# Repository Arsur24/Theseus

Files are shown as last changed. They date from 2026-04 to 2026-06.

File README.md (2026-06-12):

# Theseus
This repository will cover the documentation for RoboCup Junior Maze team Theseus.
The repository is structured into 3 main categories: mechanical, electronics, and coding.

## Overview of system architecture
Our team participates in the RoboCup Junior Maze challenge, where the goal is to navigate throughout a randomized maze, detect victims, dispense rescue packages, and navigate the maze. From a high-level view, we utilize a hybrid control architecture, which is comprised of a Deliberative layer and a reactive layer. The Deliberative layer focuses on the high-level planning of the robot's movement, such as mapping and pathfinding, whilst the reactive layer focuses on keeping the robot's movement stable, and also to detect victims. 
## Electronics
Our team has experimented with a variety of different sensors and electronics, and we found that I2C sensors produce the best results due to the organizational advantages of utilizing a single communications protocol( as opposed to using many different protocols), as well as the reduction in the amount of wiring needed, saving time for more important work. We use the Vl53L0x TOF sensors(Fig 1) due to its ease of programing and its accurate sensing.
Vl53l0X TOF
For color detection, we use the TCS34725 as it is much more reliable than other non-I2C color sensors( such as the OSEPP arduino color sensor which uses digital pins). Some teams prefer to use a custom designed photoresistor circuit for customizibility, but we regard that as overengineering in the context of the robocup rescue maze challenge.
TCS34725

Unlike other some other teams, which solely use distance sensors to accurate travel distances, we use magnetic encoders to measure the direction travelled. Last year, we used the MPU6050 gyro, but we switched it out in favor of the adafruit BNO055 9-dof IMU because of the MPU6050's tendency to drift( lack of accuracy) and also because the BNO055 returned angular position rather than angular velocity which needed to be integrated. However, the BNO055 has a 0-360 wraparound, which complicated programming a bit( as values can jump suddenly from 359 to 0).
## Code
The robot uses a object-oriented structure for its programming, ensuring the code is well organized and not messy. There are classes for motors(motors.h) and sensors(gyro.h) to package low-level functions for use in more complex programs. We also have a general use PID class(PID.h) for control of the robot. For its decision making, a state machine software structure for its main decision making. The states are centered around each tile, looping everytime it enters a new tile. There are 9 states:  SENSE_TILE,
UPDATE_MAP, PLAN_NEXT, VICTIM_DETECT,EXECUTE_MOVE, BOTCHED_TURN_RECOVERY, BACKPEDAL, PAUSE, RETURN, each triggering at the completion of the last state. The robot stores the data in each tile in a mazeTile object, which is a bitset to save precious memory space. The robot is initialized with a 20x20 array of empty mazeTile objects that is filled in as the robot traverses the maze. Our team has recognized the importance of being able to return to the start of the maze, as that would double the points scored by deploying rescue kits to victims. For the robot to do so, we implemented a BFS algorithm that allows the robot to find the shortest path to its starting point.
# Optimization and allocation of memory.
The Arduino Mega(

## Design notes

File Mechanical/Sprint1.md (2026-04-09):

## Goal

The goal for this sprint is a part of a major goal, which is redesigning a V2 bot. This sprint focuses on redesigning the chassis to a more space efficient version, while retaining the suspension design that we learned from S3R5 team. A secondary target of this sprint is to ensure the cabling of the motor wires are done correctly, to avoid any unnecessary tension on the connectors. Key indicators to the success of my goal:

- There is sufficient space for wiring in upper layers
- Optimal first layer space utilization (enough space to place a dropper)
- Ground clearance (more than 2cm, the largest obstacle size)
- Cables have adequate routes and avoid tension

#### Problem:

The current chassis has the motors mounted *above* the base layer, which results in space inefficiency. Less space is able to be used for the mounting of the MUX and the stepper motor, which results in cabling difficulties. Additionally, the battery was meant to go in the space in the center, but is blocked by cables.



Another major issue is the disorganized cabling of our previous robots. In the design process of these previous iterations, cabling strategies were ignored while designing the robot. This needs to be fixed for our newer version, making strategic cabling decisions to avoid clutter. 

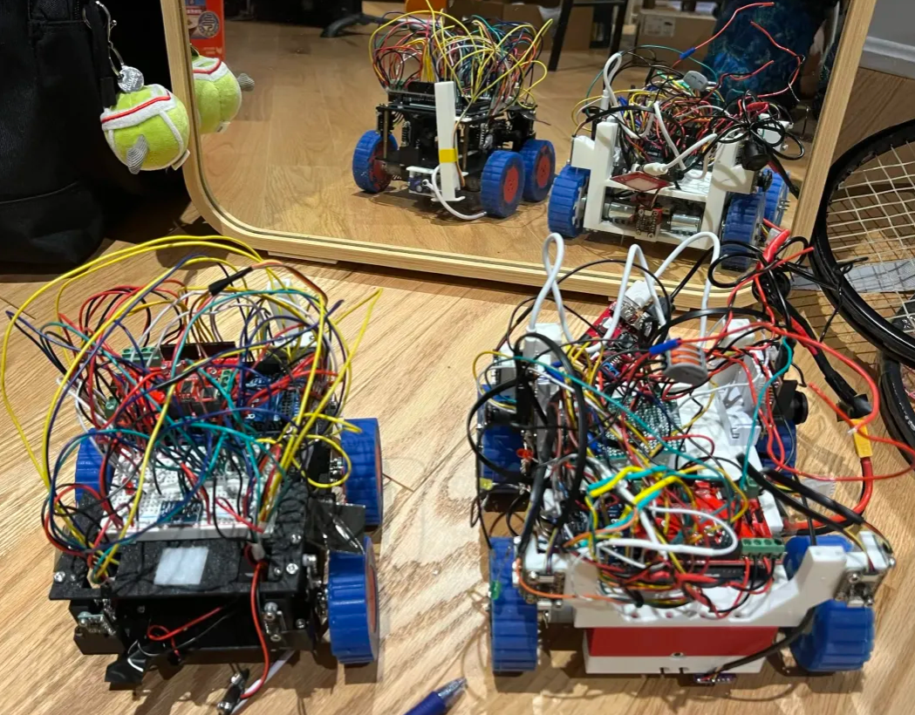
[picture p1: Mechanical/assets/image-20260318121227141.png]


## Research:

**Suspension reference**

At RoboCup Americas 2025, we met S3RS team. They had a suspension mechanism where their suspension shaft was suspended by two panels, with a dead axle shaft in between. Their design was simple yet effective, with the only necessary parts to support the suspension being 2 bearings, and a shaft. 

<table width="100%">
  <tr>
    <td width="50%" align="center">
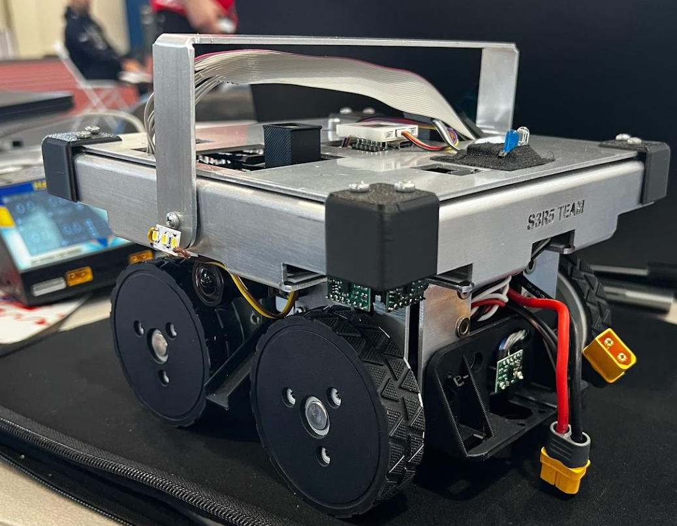
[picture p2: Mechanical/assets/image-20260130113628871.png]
      
    </td>
    <td width="50%" align="center">
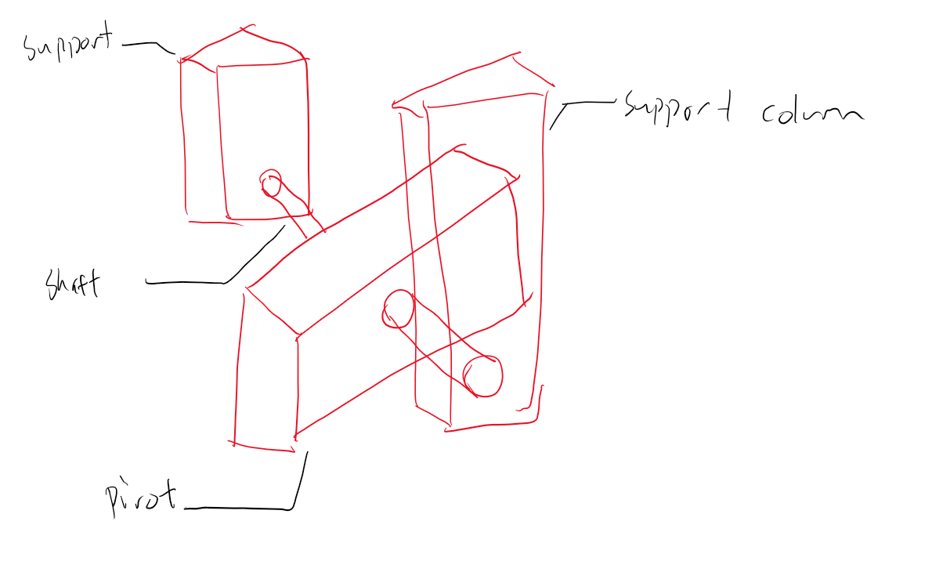
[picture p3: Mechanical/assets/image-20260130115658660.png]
      
    </td>
  </tr>
  <tr>
    <td align="center"><h5>S3R5 Team Robot</h5></td>
    <td align="center"><h5>S3R5 Team design illustration</h5></td>
  </tr>
</table>

**Dead Axle**

While researching the best way to mount the suspension, I considered a strategy that I've seen widely used in robotics competitions, such as FRC and FTC. The mechanism is a dead axle. In a dead axle, there is a fixed axle that doesn't rotate, while the rotating object is mounted with bearings, freely moving on the axle. There were many key advantages to this, but the most important factor was that a dead axle prevents **Torsional Stress** from a rotating axle. In my application, this is ideal, since I wanted to created a strong shaft that wouldn't break under constant use.

<table width="100%">
  <tr>
    <td width="50%" align="center">
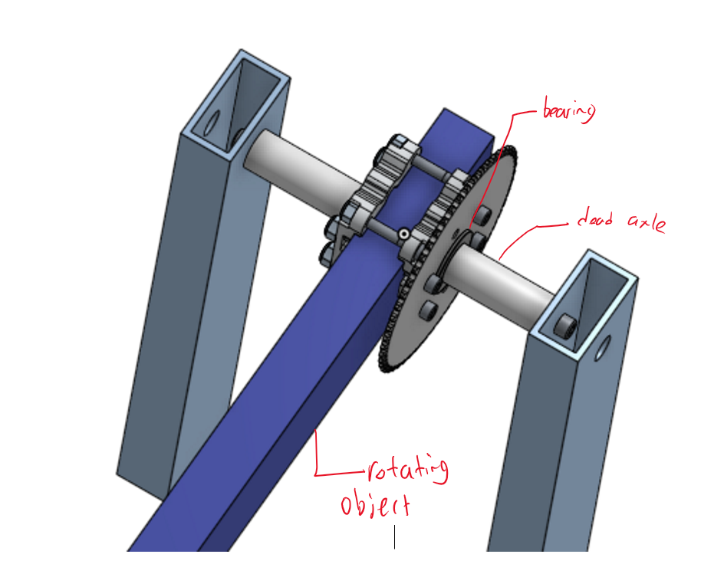
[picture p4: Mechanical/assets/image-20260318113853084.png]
      
    </td>
    <td width="50%" align="center">
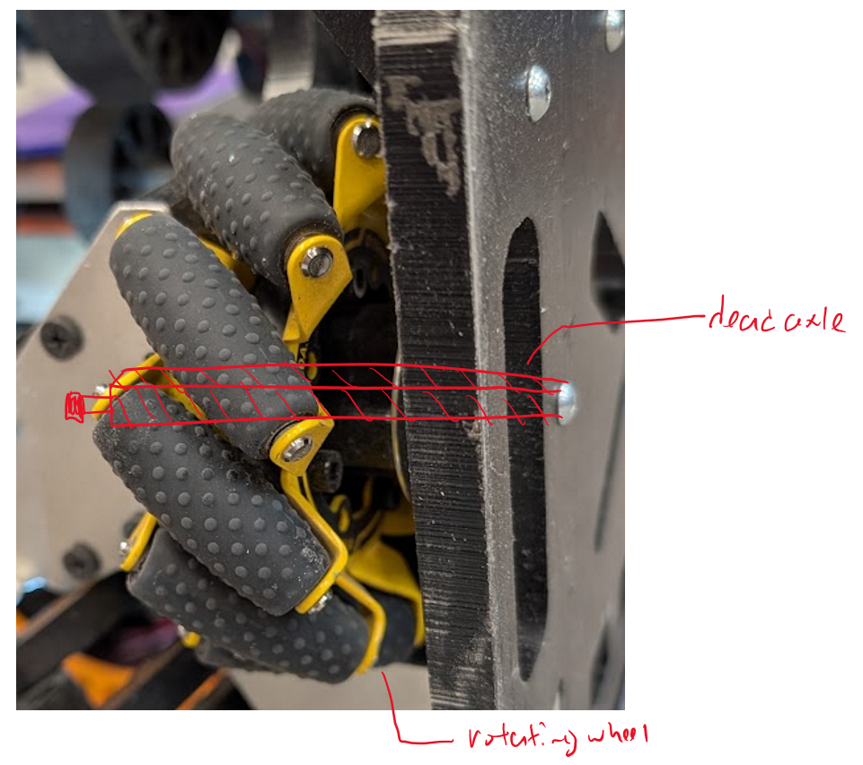
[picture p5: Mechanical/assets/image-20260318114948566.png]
      
    </td>
  </tr>
  <tr>
    <td align="center"><h5>FRC Dead Axle</h5></td>
    <td align="center"><h5>FTC Dead Axle</h5></td>
  </tr>
</table>

Both of the examples above showcase the strength of dead axles. They are a component that I'm familiar with using, with a perfect fit to my application. 

**Strain Relief**

While looking through techniques on relieving cable strain, I came across a design on Wikipedia. Strain relief was provided to the cable by having it turn a corner. We implemented a similar design onto our robot, with "posts" for the cables to string around. This design prevents any pulling on key connections. 
<table width="100%">
  <tr>
    <td width="50%" align="center">
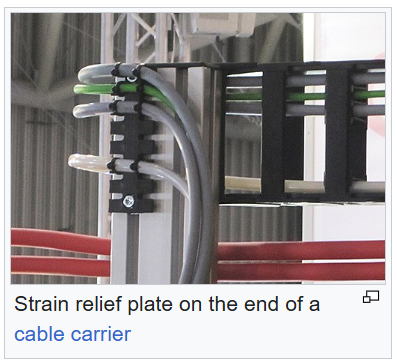
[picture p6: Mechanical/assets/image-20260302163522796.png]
      
    </td>
    <td width="50%" align="center">
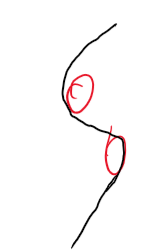
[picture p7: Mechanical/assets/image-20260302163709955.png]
      
    </td>
  </tr>
  <tr>
    <td align="center"><h5>Industry Reference</h5></td>
    <td align="center"><h5>Sketchn</h5></td>
  </tr>
</table>

## Ideation:

**Chassis structure**

Design the chassis in such a way where the motors go *under* the bottom layer, leaving more space for mux, cabling, and the battery.



- In this chassis design motors will be mounted underneath
- This creates a space between first and second layer, which is perfect for mounting a dropper

**Suspension Constraint Structure**

Reformat the position of the suspension constraint wedge to save space underneath the robot. If this isn't done, the changes to the motor positions are pointless. 

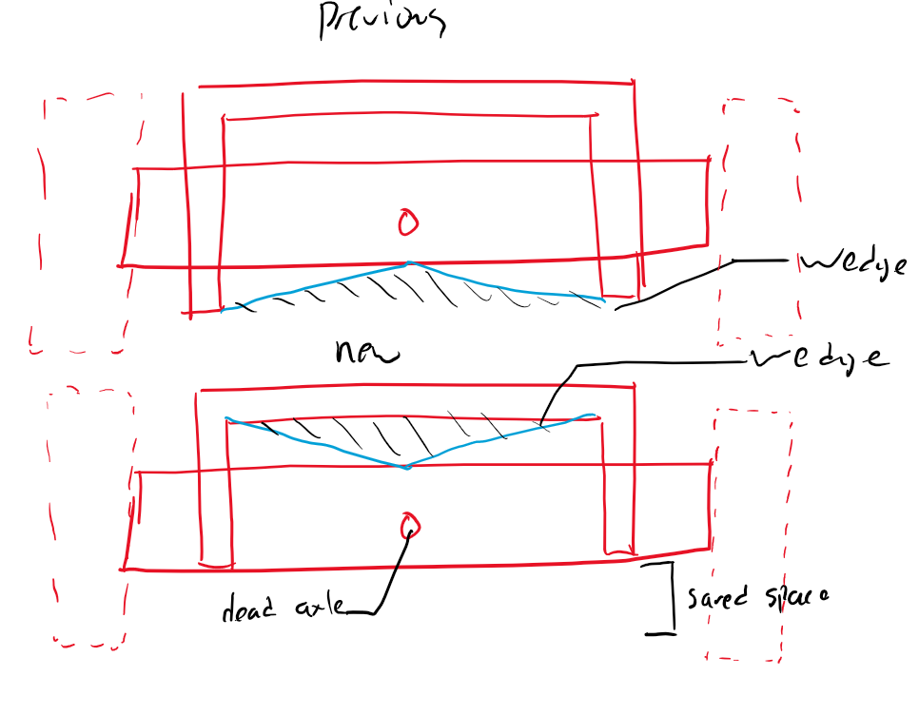
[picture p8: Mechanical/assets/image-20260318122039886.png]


- There is significant space saved from moving the wedge to the top
- Wheels can decrease their diameter, shrinking the sizing of the robot. 

**Strain Relief**

The goal of this is to make a post that is structurally rigid, and gives adequate space for all cables to fit through. 

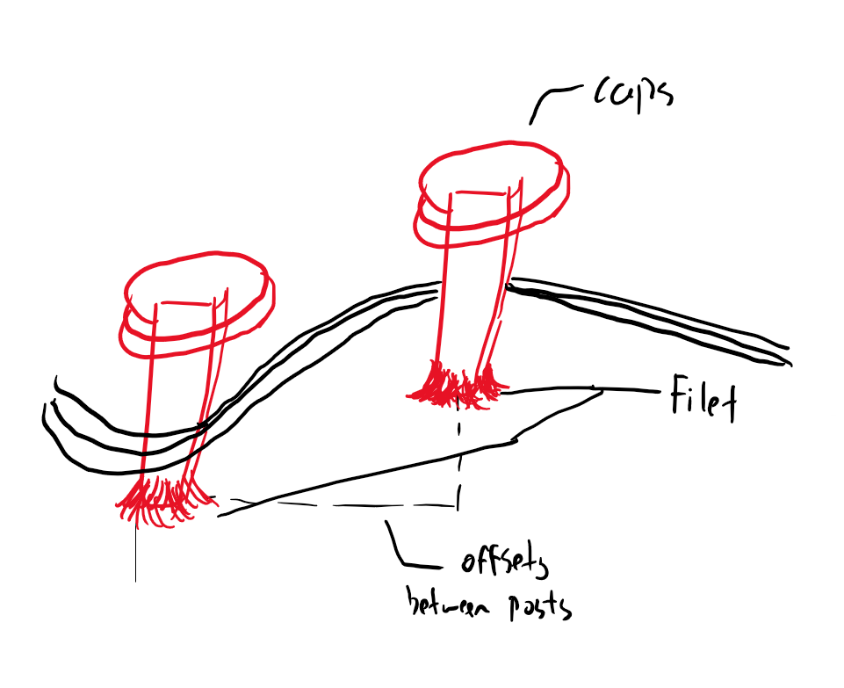
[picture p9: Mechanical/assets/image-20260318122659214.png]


- Caps are added to posts to prevent cables from slipping out
- Offsets are created, so no extra strain is created on cables, only relief
- Filets on bottom of posts to improve structural rigidity

# Daily Documentation

This section will include more reflection on my design choices, and how I adapted the design through testing (in cad, needed to resize dimensions the more I designed). 

## 2026/01/16

Today's Goal: 

- Plan out the ideas for the spring, they are shown above!
- Start the framework to figure out dimensions for the new chassis. Dimensions include:
  - Wheel size
  - Ground clearance
  - Length
  - Width

#### Chassis Side Profile:

- 2cm of ground clearance after motors are mounted
- 18cm chassis length
- 7cm wheel diameter

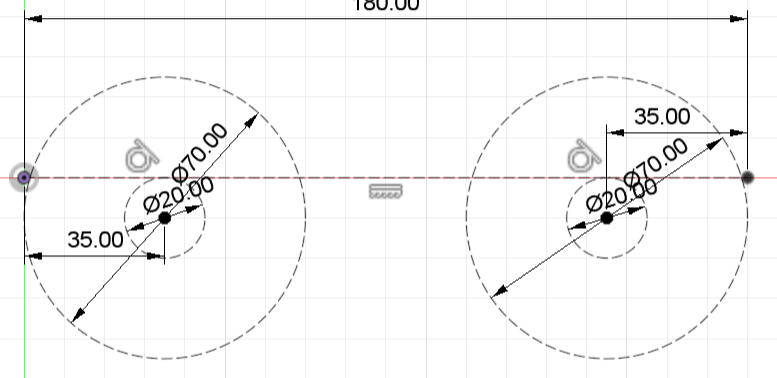
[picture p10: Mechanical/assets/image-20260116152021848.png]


#### Suspension Front Profile:

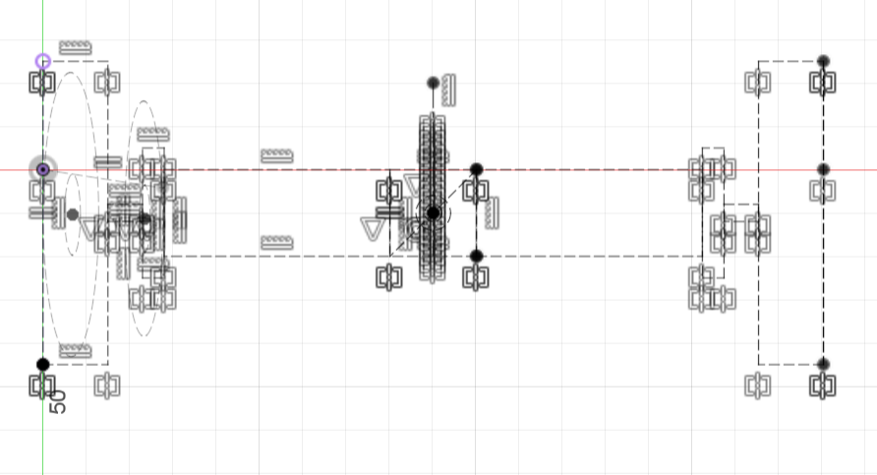
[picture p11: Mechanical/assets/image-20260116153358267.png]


## 2026/01/20

#### Today's Goal:

- Create chassis base
  - Space for battery mount
  - Adjust chassis sizing

#### Full Chassis:

- Battery mount packaged to fit under the base layer to give more space
- Wheels resized to 80cm to give 2cm of ground clearance
- Chassis lengthened to 195cm to fit battery

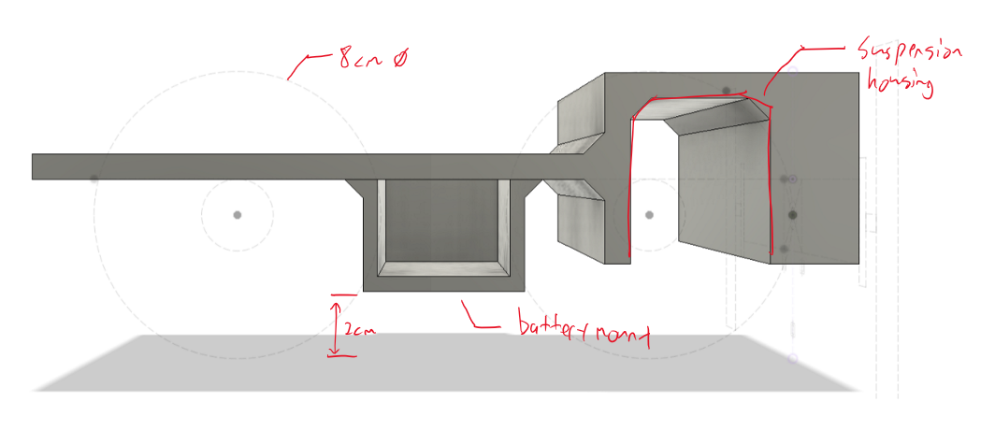
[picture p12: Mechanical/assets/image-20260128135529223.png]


## 2026/01/21

#### **Today's Goal**: 

- Create suspension axle
  - Suspension axle should have the motor mounts built in
- Create integrated motor mounts for back wheels
- Cabling
  - Use friction posts to provide relief for connections

#### **Suspension axle**:

- Added press fit for bearing. The measurement for this is the exact diameter of the bearing, with 1mm of clearance for depth. (this press fit has been tested on a previous design, and works phenomenally)
- Integrated motor mount saves space

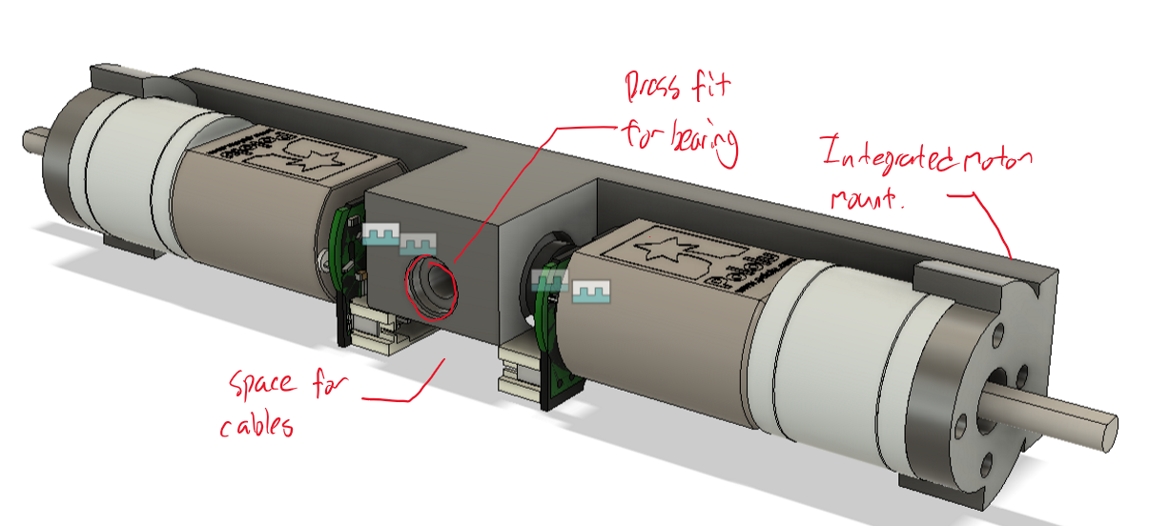
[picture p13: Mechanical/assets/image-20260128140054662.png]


#### Back wheel:

- Works as it needs to do

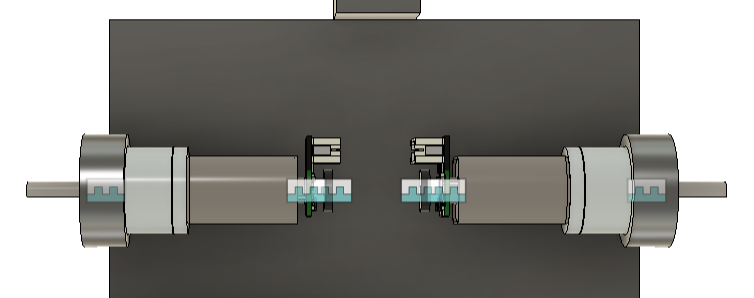
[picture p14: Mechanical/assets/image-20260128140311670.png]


#### Cabling:

- Cabling channel for suspension, directly under mounting point for ease of access
- 2 holes made for zip tie mounts, to secure cables
- 1mm countersink to make placing 2mm washers easier
- Strain relief posts to prevent any pulling on motor connection

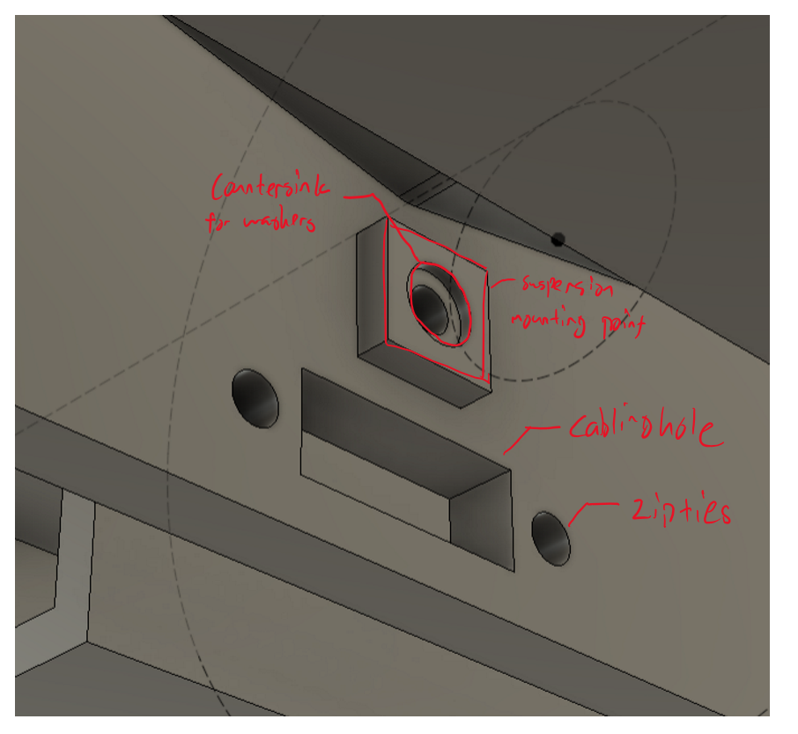
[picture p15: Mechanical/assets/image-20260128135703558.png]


<table width="100%">
  <tr>
    <td width="50%" align="center">
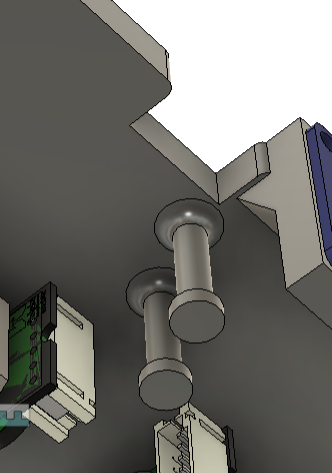
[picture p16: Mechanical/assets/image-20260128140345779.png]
      
    </td>
    <td width="50%" align="center">
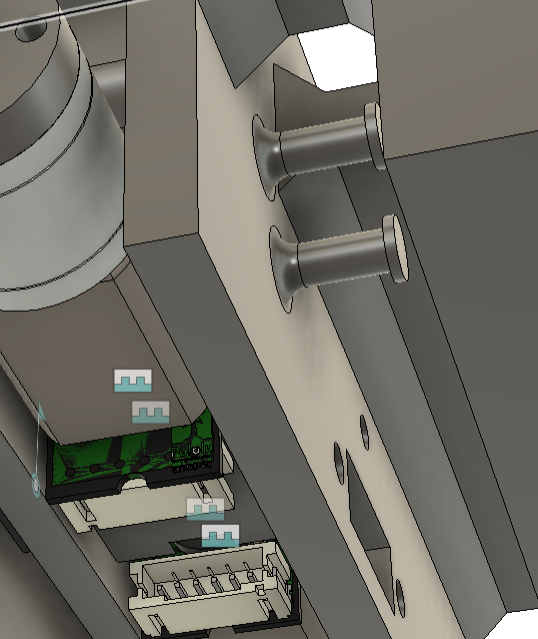
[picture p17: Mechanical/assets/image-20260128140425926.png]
      
    </td>
  </tr>
  <tr>
    <td align="center"><h5>Cabling guides for back motors</h5></td>
    <td align="center"><h5>Cabling guides for front motors</h5></td>
  </tr>
</table>

## Finished Design/Critique

The suspension reformatted chassis and suspension wedge was very successful. There is lots of space beneath the chassis, to provide ground clearance of obstacles. The repositioning of the wedge makes it fit seamlessly with the whole design.

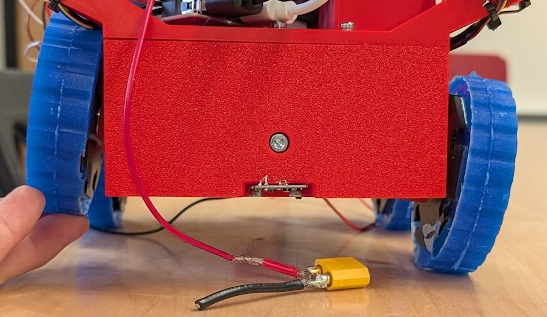
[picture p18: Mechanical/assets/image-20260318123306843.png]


The strain relief posts did exactly what they were needed to do. As you can see, the lengths that I have set here were correct, and there is no further strain on the motor. However, the posts are a little bit short. This wasn't considered when I was designing the part, so the quantity of cables passing through will be noted for future designs.

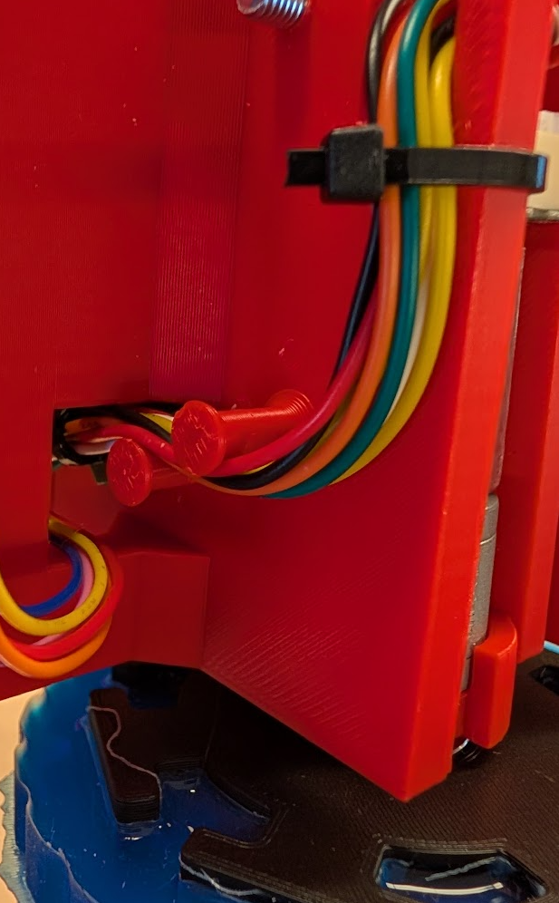
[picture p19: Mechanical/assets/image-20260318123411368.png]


# Conclusion

This design was very successful. Now that the space at the bottom layer has been cleared, there is enough room to create a design for a dropper on the bottom layer. This will lead to significant space saving, aiding us in our ability to make our robot more compact and modular.

The cabling has been significantly improved, with minimal strain on the motors. Future design choices should also consider the amount of cables traveling through, scaling the size of the post from that. 

**Next Steps**:

- Create a dropper design to fit with this current design 
- Add second layer, with cabling features. 
- Create distance sensor mounts
- Design wheel casting molds.

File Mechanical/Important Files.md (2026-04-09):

## Polulu 195:1 Metal gearmotor

https://www.pololu.com/product/3493

Orthographic Sketch:

Our motor length: 52.2mm

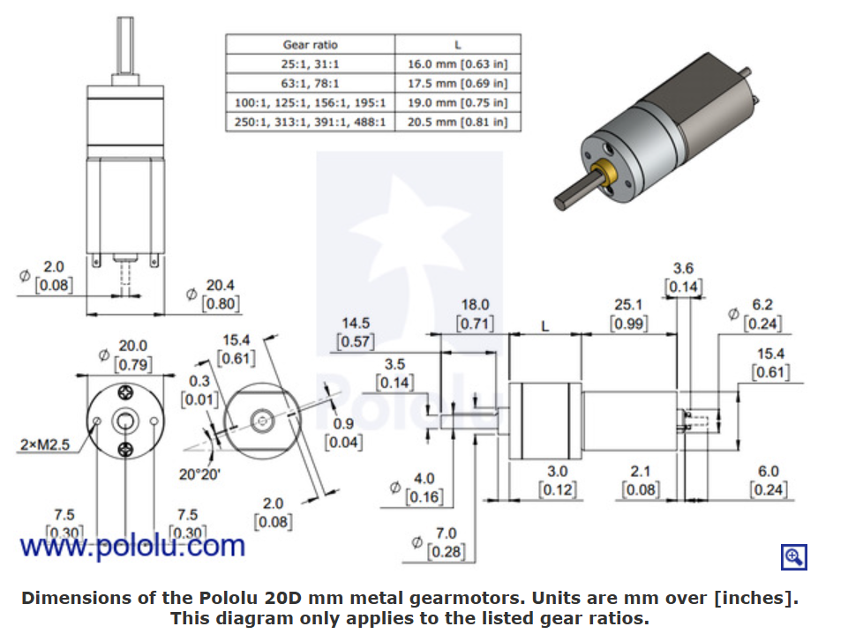
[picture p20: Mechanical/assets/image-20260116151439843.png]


# Pololu Universal Aluminum Mounting Hub for 4mm Shaft, M3 Holes

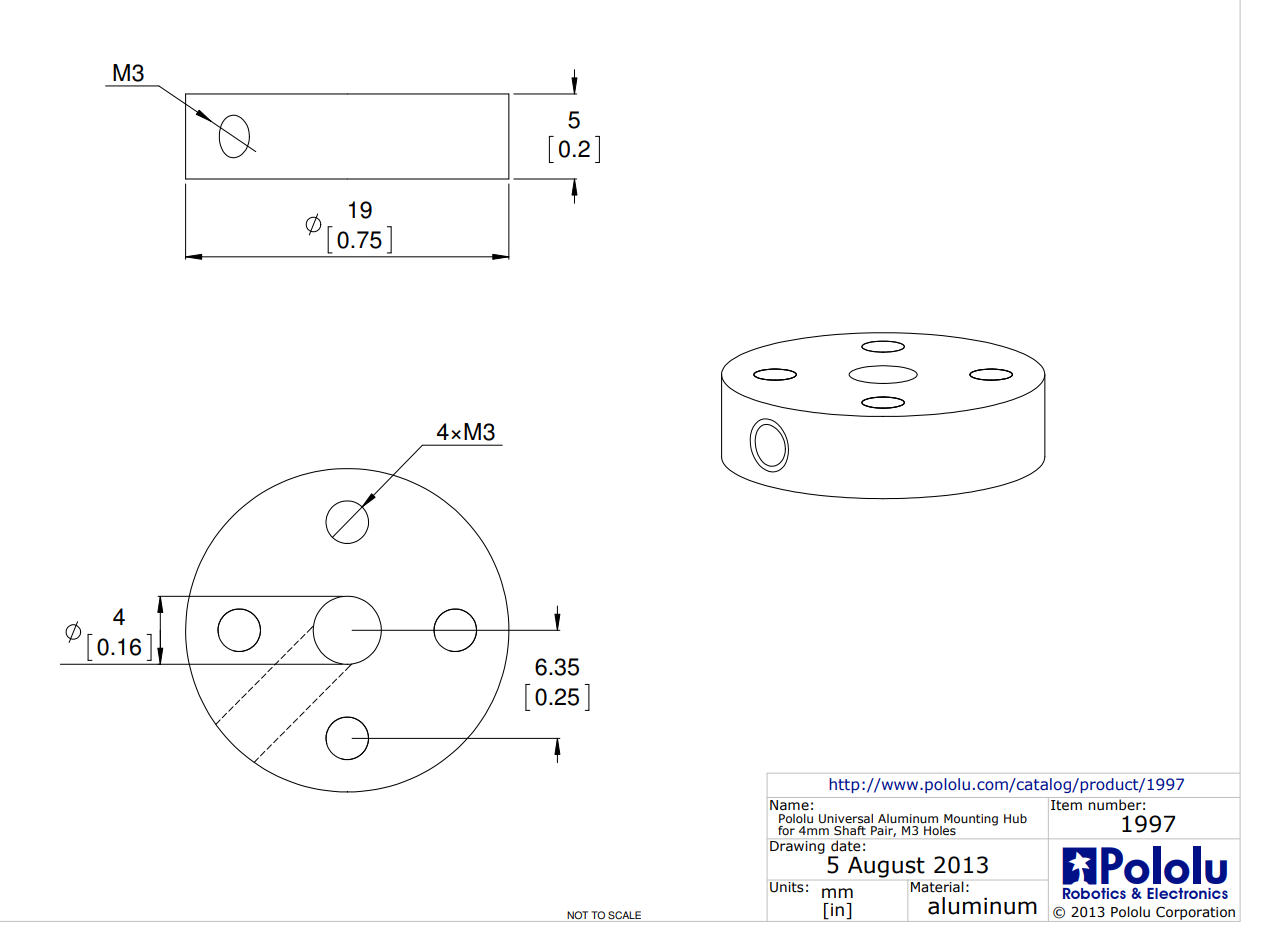
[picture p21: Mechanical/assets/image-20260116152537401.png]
https://www.pololu.com/product/1997#lightbox-picture0J1106;main-pictures

# Ball Bearing

### Steel Flanged, Open, Trade Number 74

https://www.mcmaster.com/57155K437/

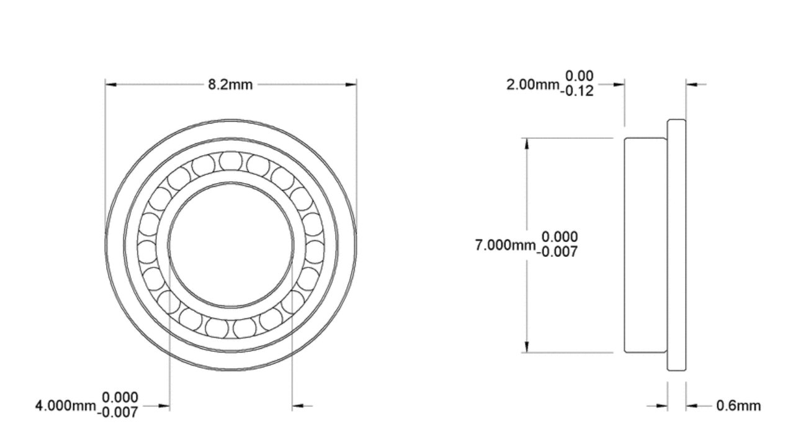
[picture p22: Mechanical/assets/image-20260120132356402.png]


# 28BYJ-48 Stepper Motor

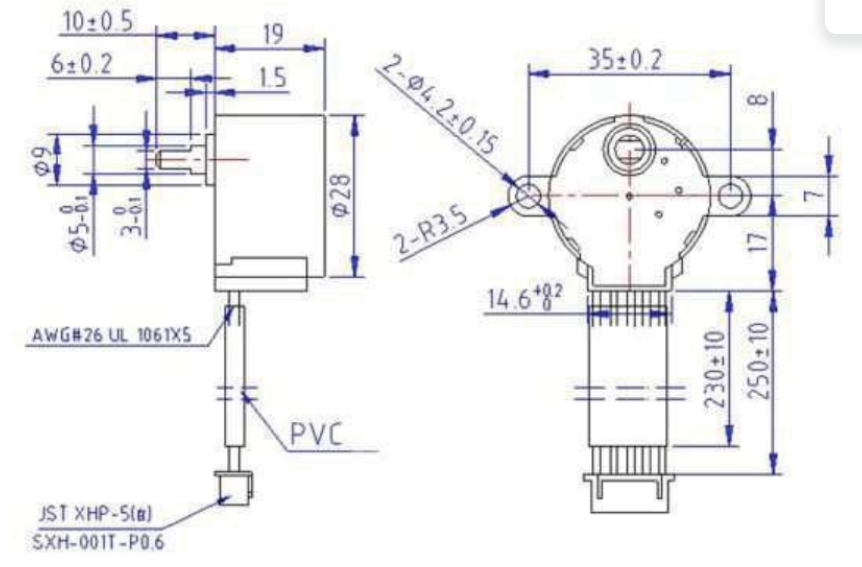
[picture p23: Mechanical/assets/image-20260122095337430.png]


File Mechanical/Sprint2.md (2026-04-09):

# Sprint 2

## Goal

The goal for this sprint is to create a cube dropper can fit into the space between my bottom layer and my second layer. This will properly utilize our space, giving us more room for cabling and other key items on the second and top layer. Additionally, the design needs to funnel the cubes into the 15cm square, with chutes that don't block the camera. The key points to determine the success of this goal are:

- Dropper fits within the small space between the first and second layer
- Dropper can index effectively (drop packets in the correct order)
- Dropper puts cubes within the 15cm radius that the packets need to be in. 

## Research

**Pez Dispenser**

[Google Patents Link](https://patentimages.storage.googleapis.com/fd/19/9d/2968bb013a5a3a/US2620061-drawings-page-1.png)

A PEZ dispenser is a mechanism used to dispense little tablets of mints, later turned into candy dispensers, seen on candies.

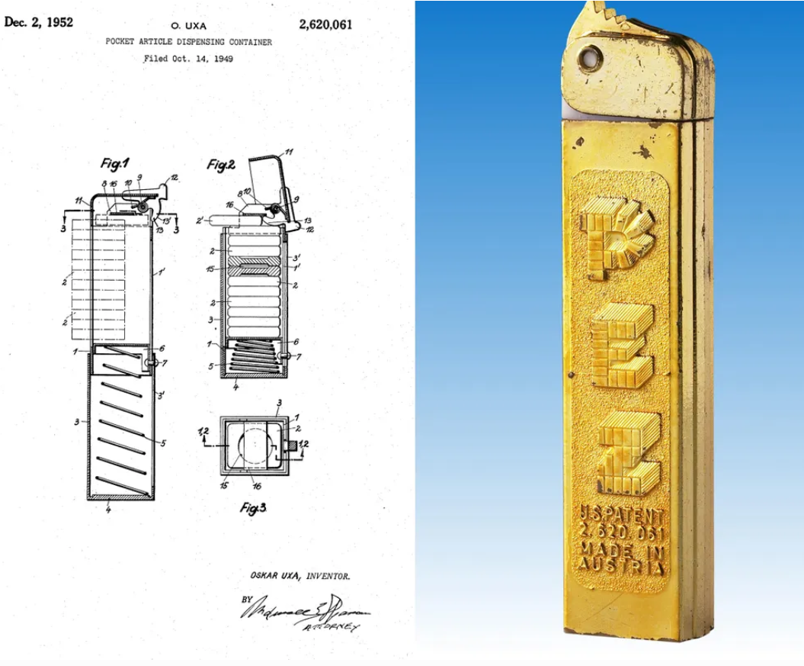
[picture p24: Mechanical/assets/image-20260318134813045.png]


This design is extremely simple. It uses a spring to push the tablets into position, then a kicker to eject them. This cycle allows for one by one ejection of tablets. 



**Turntable-Style Dropper**

[Gumball Mechanism Explanation (Youtube)](https://www.youtube.com/watch?v=Q3ZeUNDg4fQ)

One unique mechanism found in a gumball machine is a turntable style dispenser. A turntable with cutouts to fit gumballs is mounted on a rotating axle. The gumball fits well into the cutout, and is rotated by the turntable, until it reaches a dispensing gap, causing the ball to fall through. Because of the wide presence of gumball machines, this design has proven its reliability. 



At RoboCup Americas 2025, the best performing robot had a very similar design, with a turntable containing square cutouts for cubes. This showed our team that this design style was feasible for small RoboCup maze robots. 



This design was very strong in many ways, including:

- Turntable design allowed us to drop cubes on both sides
- Very compact packaging, fits nicely onto one layer
- Simple to load

**Paddle Dispenser**

[Patent Application](https://www.patentsencyclopedia.com/app/20140183217)

This paddle mechanism stacks the cans it's dispensing. It uses gravity to let these cans flow downwards, towards a paddle, which dispenses one can at a time. This simple mechanism is very robust. 



## Ideation

**Turntable Dropper**

This design uses the turntable mechanism. It is a very simple mechanism, with a stepper motor turning a large table with cubes on the outer edges. There are two holes, and two chutes, which allow for the selection of which side to drop. The chutes help funnel the cubes towards the 15cm radius of the rescue packet zone. 



Pros:

- Simple and robust design
- Side selection
- Flat (can fit nicely onto a layer)

Cons:

- Takes a large amount of surface on a layer
- Takes longer to load

**Paddle Dispenser**

The paddle dispenser places cubes in a stack, using gravity to funnel them towards a paddle area. The paddle ensures that only one cube exits at a time. It acts as a pushing mechanism, ejecting the cube towards the 15cm zone. 



Pros:

- Simple to load
- Takes up less space on one layer, instead, just vertical space

Cons:

- Placement of actuator for paddle is difficult
- Geometry of paddle is difficult to design around
- No side selection

**Inverted Pez Dispenser**

This design also uses a stack mechanism to hold all the cubes. A pusher ejects one cube at a time, allowing another cube to flow in after the pusher exits the area. 



Pros:

- Simple to load
- robust design, unlikely to malfunction

Cons:

- Pusher takes up a lot of space
- No side selection

**Final Chosen Idea**

The final chosen idea is a turntable style dropper. This design provides one necessary component that the others don't, which is the side selection of where to drop the cubes. This saves time, because the robot does not need to spin 180 degrees to eject a cube in the right location. 

Additionally, the packaging of this dropper will fit nicely into the space between my two layers, with space in the bottom for the motor. There will be large openings for cubes to drop through, and chutes to funnel them close to the wall.



An extra design addition to help improve the consistency of this mechanism are guide rails. There is no lateral movement constraint on the turntable except for the motor. The guide rails take away the forces that could potentially damage the motor, helping to ensure the longevity of this design. 



## Prototypes, Testing & Critique

Our previous robot used the same design, and there were many things that we learned from the use of this design. These lessons will help us prevent future mistakes from happening with our next design. 



Firstly, this design took up a large amount of space, because of the positioning of the motor. Since the motor was embedded within the dropper, there needed to be a large amount of excess material and space dedicated towards its fitting. 



Another major issue with this design was the engagements of the guide. When designing, no space was left between the dropper and the top layer of the base. This meant that the dropper was slightly elevated over where the guide was supposed to be, preventing it from engaging. 



The height of the chutes also posed a major problem in this design. When dropping from such a high height, there was a potential for the cubes to bounce, and roll away from where they were intended to drop. 



**Next Steps:**

The first decision is to place the motor beneath where the dropper is. This saves a lot of excess space, and fits perfectly with my chassis design. 



Secondly, there will be some clearance between the top layer, and the guide. This will allow for full engagement of the guides, without any other contact interfering . 



Thirdly, the dropper will be placed at a lower height, to prevent the cubes from accidentally rolling during the dropping phase. 



## Final Design

The final concept is extremely compact, and space efficient. Key aspects to note about this design are:

- 19mm x 19mm hole for 10mm x 10mm cubes to fall through
  - Allows a larger space for cubes to rotate around, to prevent any jamming
- Two chutes
  - **Allows for indexing of which side to drop out, to prevent full robot rotations, saving time.** 

- 1mm clearance between dropper and ground
  - Prevents craping on any countersunk screws, and gives tolerance to work with
- 8mm x 4mm triangular spikes
  - Allow for an extremely large contact surface with the dropper
  - Creates the stability needed to prevent lateral movement
- Stepper motor mounted on the bottom, with press fit shaft
  - **Mounting the stepper motor on the bottom saved lots of space, allowing for a completely empty 2nd layer to place wiring and other components**
  - Press fit is the simplest method to connect these surfaces, saving the space that a motor mount would've taken
- Steep chute angle to align with wheel position
  - **Allows the cubes to be dropped outside where the wheels are positioned, staying in the 15cm circle that rescue packets need to be in**





# Conclusion

This design is very effective, and built on our past experiences from other dropper style designs. It fits in an extremely compact format between two layers, allowing for full development on the second layer. However, due to rule changes, the maximum amount of cubes has been changed to 8. This gives access to a wide variety of previously unusable designs. In future sprints, I will investigate different mechanisms to see if there is any more efficient way of packaging the dropper.

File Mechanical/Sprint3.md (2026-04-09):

# Sprint 3

## Goal

The goal for this sprint is to create a rescue packet that is weighted, helping it stay within the 15cm radius where the points are evaluated. Key indicators for success are:

- Fits in a 10x10x10mm package

- Can be 3d-printed, or simple to assemble
- Stay within 15cm radius when dropped

## Research

**Loaded Dice**

[Youtube Short](https://www.youtube.com/shorts/_t8j6g0dd9Y)
[TrickDice.com](https://trick-dice.com/product/double-trouble-face-loaded/)

A loaded dice places an extra weight on one face of the dice, incentivizing this roll more. The youtuber Engineering Addiction ran tests with this dice, finding that the loaded dice had a 41% chance of landing on the weighted side, significantly higher than normal 16.67%. The hidden weight used in this design is an iron insert, which is a relatively dense metal, at 7.874 g/cm³ (NIST). 



**Roly Poly Toy**

[Youtube](https://www.youtube.com/watch?v=QMjszY40BoU&t=17s)
[Computer Aided Geometric Design](https://doi.org/10.1016/j.cagd.2016.02.001)

A roly-poly toy is a self righting doll, which can return to an upright position no matter how you move it. There is a hollow cavity with a weight inside, which is used to correct the cube back into equilibrium. The weighted ball and the size of the cavity are tuned to ensure the ball can reach properly. The wobbling of the toy helps dissipate energy given into the system, which keeps the toy in place. 

 

**Viscoelastic Material**

[Science Direct](https://www.sciencedirect.com/topics/materials-science/viscoelastic-material?utm_source=chatgpt.com)
[Sorbothane Inc.](https://www.sorbothane.com/technical-data/articles/what-is-viscoelastic-material/)

A viscoelastic material exhibits both elastic and viscous properties. They begin by absorbing forces like an elastic, then dissipate them like a viscous Newtonian fluid. These properties allow for the object to receive impact, and spread it out. Common examples are cornstarch and water, or silicon. 



**Cube Physics**

[Chaos: An Interdisciplinary Journal of Nonlinear Science](https://www.researchgate.net/profile/Marcin-Kapitaniak/publication/234029725_The_three-dimensional_dynamics_of_the_die_throw/links/00b49528f8de4c42cb000000/The-three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)

When dropped, a cube tends to tumble rather than roll smoothly. These tumbles cause repeated impacts which help dissipate energy through inelastic impacts governed by restitution and friction. The nature of the cube helps it travel less distance from the point its dropped, compared to other geometric shapes. 



## Ideation

**One sided weighted cube**

This design takes inspiration from the loaded dice, having a weight towards the bottom which encourages the cube to land on one side, preventing it from rolling far. The metal should be something with a heavier weight, like steel or tungsten. 



Pros:

- Proven that it works (41% chance of staying on one side)
- Metal is easy to find

Cons:

- Metal can't be too large, because our cube is very small. If metal is too large, the walls are too thin, and the cube will break over time. 
- Although the cube is more inclined to stay on one side, this design isn't the most optimal, as the purpose of a cheating dice is that it's not extremely obvious, meaning there is still room to improve

**Roly-Poly Cube with Weighted Sphere**

Following the roly-poly doll design, this design will prevent the ball from rolling. The ball is heavily weighted, with a large cavity, so no matter which side the ball lands on, the roly-poly effect will work. 



Pros:

- Roly-poly dolls are designed to stay on one side, meaning this design will be very effective
- Metal ball can get very heavy, helping further

Cons:

- Walls would be very thin, if ball is large
- Ball is difficult to insert while 3d printing, leading to sub-optimal cavity design

**Roly-Poly Cube with Metal Pellets**

This design follows a similar idea as the roly-poly weighted ball, but uses heavy metal pellets instead. These pellets equate to a similar weight, and are much smaller than the cube. There is a large cavity, allowing the pellets to fit in the space. 



Pros:

- Pellets are easy to insert into design while 3d printing
- Cavity can be smaller, but still achieve the same effect

Cons:

- Pellets cannot be magnetic, because if they are, printing has to be careful so that the pellets don't stick to the nozzle
- Pellets are hard to find :(

**Silicon Cube**

Silicon is a viscoelastic material, so making a whole cube out of silicon would allow for the impacts to be dampened, preventing them from rolling extremely far. 



Pros:

- Simple to make, only need to cast silicon
- Doesn't roll far because of material properties

Cons:

- Depending on the friction properties of the type of silicon cast, the cube may have too much grip, and the dropper won't be able to move it

**Final Chosen Idea**

The final chosen idea is the roly-poly design, with metal pellets. The main reason for this design being chosen over the others is because

1. Roly-poly is a proven toy technology (I will test this more later)
2. Pellets are easier to work with, because I can design the packaging for the printing of the object in a simpler way
3. Pellets allow ANY SIDE to be weighted better than the other sides, compared to the one side weight of the cube. 

## Prototypes, Testing & Critique

I prototyped the roly-poly idea with carboard cube, which allowed for a hollow center. I then placed little bolts to simulate the pellets that would be placed inside, then sealed the cube with hot glue.



This simulated the roly-poly physics, which allowed me to see if the weighted distribution actually affected how much the cube rolled.

**Results**:

What worked:

- When dropped from a height of ~3 cm, the cube didn't roll very far, which would keep it within the scoring zone

- The sealing method worked well, because I was able to have the walls of the cubes created, making a housing for the pellets, before sealing the top.
- This prototype was very quick to design.

What failed:

- Because of the uneveness of my cutting, the cube wasn't very even, with some sides having an acute angle (instead of 90 degrees). This caused the weight over the unbalanced area to allow for the cube to tilt over, rolling more than intended. 
- The nuts have a lot of space inside, due to their holes. This resulted in a lighter weight, which didn't create the best-case-scenario for anti-roll. Since the COG was made higher, the cube would be less stable.
- Being made from cardboard, the cube itself was also light, which decreased the ability of gravity to prevent it from rolling. 

**Next Steps**:

1. *Use smaller and heavier weights:* By using smaller and heavier weights, I am optimizing the space in the roly-poly design, lowering the COG, and helping it roll less. A very good material choice for this is tungsten, because it is extremely dense. ($19.3g/cm^3$).



2. *Create a uniform cube:* Make sure that the cube is a uniform cube, so that it doesn't have a tendency to do an extra roll. This can be achieved by 3d printing the cubes. 



3. *Increase the size of the cavity:* By increasing the size of the cavity, I can fit more cubes in, further improving the effectiveness of my roly-poly design, by lowering the COG even further. I can do this using 3d-printed walls because of their super thin structure. (0.4mm per layer. )

## Final Design

The final concept is extremely compact, and space efficient. Key aspects to note about this design are:

- 19mm x 19mm hole for 10mm x 10mm cubes to fall through
  - Allows a larger space for cubes to rotate around, to prevent any jamming
- Two chutes
  - **Allows for indexing of which side to drop out, to prevent full robot rotations, saving time.** 

- 1mm clearance between dropper and ground
  - Prevents craping on any countersunk screws, and gives tolerance to work with
- 8mm x 4mm triangular spikes
  - Allow for an extremely large contact surface with the dropper
  - Creates the stability needed to prevent lateral movement
- Stepper motor mounted on the bottom, with press fit shaft
  - **Mounting the stepper motor on the bottom saved lots of space, allowing for a completely empty 2nd layer to place wiring and other components**
  - Press fit is the simplest method to connect these surfaces, saving the space that a motor mount would've taken
- Steep chute angle to align with wheel position
  - **Allows the cubes to be dropped outside where the wheels are positioned, staying in the 15cm circle that rescue packets need to be in**





# Conclusion

This design is very effective, and built on our past experiences from other dropper style designs. It fits in an extremely compact format between two layers, allowing for full development on the second layer. However, due to rule changes, the maximum amount of cubes has been changed to 8. This gives access to a wide variety of previously unusable designs. In future sprints, I will investigate different mechanisms to see if there is any more efficient way of packaging the dropper.

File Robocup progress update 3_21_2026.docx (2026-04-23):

Work completed

____________________________________________________________________________

BFS is working( Could return to start even after traversing 50 tiles).

Navigation is fixed.

- Remembers black tiles

Camera could now detect cognitive targets and letter targets.

Work that needs to be done

____________________________________________________________________________

Wire the second robot.

Test climbing navigation

Memory saving hasn’t been implemented.

Obstacle avoidance.

Issues:

____________________________________________________________________________

Power issues on the first robot

- Very faint PWM whining.
- Robot stops abruptly/ completely loses control, sensors start blinking.
- Suspected current dips.

OpenMV find_circles() misidentifies letters as circles, sending garbage data.

- Find circles is also highly unstable, dependant on lighting conditions.

Arduino sometimes fail to respond to camera detections.

- Used preliminary blob detection(faster) to tell the robot to stop sooner.
- However, theres the issue of the Arduino misidentifying blobs.

Motors 2 and 3 are slower on the new robot

- Rigorous variable-controlled testing required to diagnose issue.

Dispensing is inaccurate on the first robot.

- The stepper does not return to its original position after dispensing

Confusion between black and blue tiles

- Can be fixed by tuning, but it is strange that the color sensor records different values.

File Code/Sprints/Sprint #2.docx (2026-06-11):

Sprint #2 Continued Development

Goals:

1. LONG TERM: Complete secondary robot, including mounting and development, with functioning mechanical components and sensors, with a focus on scoring and victim detection.
2. SHORT TERM
- Wire management, develop the new robot with significantly better wire management than its predecessor
- Stepper motor control and block scoring( Baichen Luo).
- 3d Printing and assembly
- Silicone wheel casting and mold design
- Obstacle avoidance(Baichen Luo).

Documentation Research, and Development (Leo)


Mounted the suspension system for the new robot

Silicone wheels:


New wheels were designed, cast and printed(Leo)
ELECTRICAL COMPONENT OF THE ROBOT (LEO)

Goals

Make the robot's wiring more reliable and improve how the sensors work by using better wiring and adding lights to the sensors.

Wire Management and Reliability Improvements

What I Did: Replaced (SOME) solid core wires with stranded wires to make the robot more durable.

Why This Matters:

Solid core wire breaks easily at the solder joints when the robot moves and vibrates. Stranded wire bends better and doesn't break as easily. This makes the connections much less likely to fail during the competition

Removed (desoldered) the old solid core wires from the robot. Replaced them with stranded wire that's the right thickness for each sensor. Organized (some) of the wires neatly to avoid putting stress on the connections. Made sure (SOME) solder joints were secure and wouldn't break – Work in progress still

Results:

Stronger connections that won't break from movement/ unplug during competitions. Much lower chance of wires failing during competition. Slightly Cleaner and easier to work with wiring

LED Lighting for Sensors

What I Did: Added white LEDs next to all the sensors so they always have the same lighting.

The Problem: Room lighting changes between our workspace and the competition venue. When lighting changes, the sensors give different readings and need to be recalibrated. Color sensors and distance sensors are especially affected by lighting changes

Solution: Installed white LEDs next to all sensors (OpenMV CAMERA, color sensors). The LEDs give the sensors their own consistent light no matter what the room lighting is like Placed the LEDs carefully to avoid glare while making sure the sensors are lit evenly

Why This Helps: Removed the need for calibration and overcomplicating the code that barely works further. Sensors work the same everywhere. More reliable: Fewer bad readings from the sensors. Saves time: Don't need to spend time adjusting sensors before competition. Repeatable performance: Robot behaves the same way no matter where we run it

Overall Impact

These improvements help make the new robot more reliable. By fixing the wiring problems and ensuring the sensors always work consistently, the robot's electrical component now has a solid foundation for the rest of the robot to work properly during competition.

Obstacle avoidance(Baichen):

Idealization:

Architecture: I did not want to make a bloated function with lots of if loops inside, as it would be messy. Instead, I decided to opt for a state machine architecture.

https://junior.robocup.org/wp-content/uploads/2026/01/RCJRescueMaze2026-draft.pdf


My State machine has 3 states: Turn, Parallel, and backward. The robot first uses its front distance sensors to detect the obstacle( detecting is labelled in green). Based on whether the left or right sensor is blocked, the robot would choose to turn left or right until the blocked sensor is blocked. Next, the robot uses PID to go forward while paralleling, in the goal of edging towards the wall. When the robot is too close to the wall, the robot would go backward until it enough far away from the wall. States 2 and 3 keep repeating until the sensors report the robot is parallel to the wall, and can proceed forward.

( This was inspired by parking).

Product:

void obstacleavoidance(int leftright){ // leftright determines to manuver left or right.

while(true){

switch (steps){

case TURN:{

if(leftright == 1){ // obstacle at left

while(measure(7) < MIN_DIST){

motorB->run(BACKWARD);

motorD->run(BACKWARD);

motorA->setSpeed(255);

motorB->setSpeed(255);

motorC->setSpeed(255);

motorD->setSpeed(255);

}

}

else if(leftright == 0){ // obstacle at right

while(measure(1)<MIN_DIST){

motorA->run(BACKWARD);

motorC->run(BACKWARD);

motorA->setSpeed(255);

motorB->setSpeed(255);

motorC->setSpeed(255);

motorD->setSpeed(255);

}

}

fullstop();

delay(200);

motorA->setSpeed(255);

motorB->setSpeed(255);

motorC->setSpeed(255);

motorD->setSpeed(255);

delay(300);

fullstop();

delay(200);

steps = PARALLEL;

break;

}

case PARALLEL:{

PID pid(1,0,0.1);

if(leftright == 1){

while(measure(2)>=25){

double increment = pid.getPID(abs(measure(3)-measure(2))); // get close to the edge as possible.

motorA->setSpeed(constrain(100-increment,30,255));

motorB->setSpeed(constrain(100+increment,30,225));

motorC->setSpeed(constrain(100-increment,30,255));

motorD->setSpeed(constrain(100+increment,30,225));

if(abs(measure(3)-measure(2))<=5){

fullstop();

delay(200);

steps = FWD;

goto end;

}

}

}

else if(leftright == 0){

while(measure(6)>=25){

double increment = pid.getPID(abs(measure(6)-measure(5))); // get close to the edge as possible.

motorA->setSpeed(constrain(100-increment,30,255));

motorB->setSpeed(constrain(100+increment,30,225));

motorC->setSpeed(constrain(100-increment,30,225));

motorD->setSpeed(constrain(100+increment,30,225));

if(abs(measure(6)-measure(5))<=5){

fullstop();

delay(200);

steps = FWD;

goto end;

}

}

}

steps = BACKTRACK; // put switch step in front of end( always meet it)

break;

end:

break;

}

case BACKTRACK:{

Serial.println("backtracking");

if(leftright == 0){

while(measure(6)<=25){

motorA->run(BACKWARD);

motorB->run(BACKWARD);

motorC->run(BACKWARD);

motorD->run(BACKWARD);

motorA->setSpeed(100);

motorB->setSpeed(100);

motorC->setSpeed(100);

motorD->setSpeed(100);

}

}

else if(leftright == 1){

while(measure(2)<=40){

motorA->run(BACKWARD);

motorB->run(BACKWARD);

motorC->run(BACKWARD);

motorD->run(BACKWARD);

motorA->setSpeed(100);

motorB->setSpeed(100);

motorC->setSpeed(100);

motorD->setSpeed(100);

}

}

fullstop();

delay(200);

steps = PARALLEL;

break;

}

case FWD:{

fwd(300);

}

}

}

}

Reflection:

https://www.adafruit.com/product/3317?srsltid=AfmBOorYx9HujPoq666eJgHWlfeGMB_g-yDZlW-NYIVmW3EhVjr3tpxh

The code is logically correct, but still requires vast amounts of tuning for it to work. Firstly, the Vl53L0X distance sensor has a minimum range of 30mm, which is inconvenient when dealing with distances less than that when avoiding obstacles. Secondly, the PID paralleling needs to be tuned, which would take a lot of time. The third issue( perhaps the most important of them all), is the problem that the wheels are wider than the distance sensors. This means that when the distance sensor things the robot is clear of the obstacle, the wheels are still going to bump into it. Therefore, we made the wheels less wide for the next robot to avoid this issue.


Servo dispenser(Baichen):

Idealization:

The 28BYJ-48 is a 5V stepper, and the robot is powered by a 12v power source. Therefore, I need a voltage buck to convert 12v to 5v to power the stepper.

https://www.pololu.com/product/2851

Wiring diagram:


Product:

I made a dispenser class for the dispenser.

Dispenser.h:

#ifndef dispenser_h

#define dispenser_h

class dispenser{

public:

int leftDispensed; int rightDispensed;

int incr, offset, steps_per_rev;

dispenser(int, int, int);

void rotate(int);

void dispenseLeft(char);

void dispenseRight(char);

};

using sdispenser = dispenser; // Warning! this might not work on somebody else's computer!!!

#endif

Dispenser.cpp:

#include <Arduino.h>

#include "dispenser.h"

#include <Stepper.h>

extern Stepper myStepper;

extern int medkits;

dispenser::dispenser(int _incr, int _offset,int _steps_per_rev){

incr = _incr;

offset = _offset;

steps_per_rev = _steps_per_rev;

leftDispensed = 0; rightDispensed = 0;

}

void dispenser::rotate(int degrees){

myStepper.setSpeed(7);

long steps = ((long)degrees*steps_per_rev)/360;

myStepper.step(steps);

}

void dispenser::dispenseLeft(char victim){ // clockwise

switch(victim){

case 'H':

rotate(-(incr*2+offset+leftDispensed*incr));

leftDispensed += 2;

medkits -= 2;

rotate(offset+leftDispensed*incr);

break;

case 'S':

rotate(-(incr*1+offset+leftDispensed*incr));

leftDispensed += 1;

medkits -= 1;

rotate(offset+leftDispensed*incr);

break;

case 'U':

break;

}

}

void dispenser::dispenseRight(char victim){ // clockwise

switch(victim){

case 'H':

rotate(incr*2+offset+rightDispensed*incr-11);

rightDispensed += 2;

medkits -= 2;

rotate(-(offset+rightDispensed*incr-11));

break;

case 'S':

rotate(incr*1+offset+rightDispensed*incr-11);

rightDispensed += 1;

medkits -= 1;

rotate(-(offset+rightDispensed*incr+11));

break;

case 'U':

break;

}

}

Reflection:

The Servo worked quite well, but there were a few issues. Firstly, I renamed the dispenser class to sdispenser for alphabetical reasons(Arduino IDE compiles files by alphabetical order). However, there was actually no such issue, so I switched it back. Unfortunately, the IDE thinks the sdispenser file is still there, which is not possible. Even after closing Arduino IDE and restarting the computer, the error still occurred. Therefore, I created a sdispenser.h and referenced it, and the error went away somehow. This might not work on somebody else’s computer.

Due to the servo being badly mounted, there is some “slack” before meeting the resistance of the motor, making dispensing inaccurate. Therefore, I added an offset( based on the angular size of the slack region) to compensate.

Christopher:

# Navigation and Logic Improvements

## 1. Blue Tile Avoidance Strategy

According to competition rules, blue tiles represent difficult terrain and impose movement penalties (e.g., mandatory stop) . Re-visiting such tiles unnecessarily reduces efficiency and increases the risk of lack of progress (LoP).

To address this, the navigation system was extended with state-aware tile classification:

- A new attribute was added to the MazeTile class:
  - isBlue
  - visitedBlue

### Initial Implementation

- When a tile is detected as blue:
  - It is marked in the map.
  - The navigation algorithm avoids revisiting it during BFS/path planning.

### Issue Encountered

- The robot could become trapped when:
  - The only available path required passing through a previously visited blue tile.

### Final Solution

A conditional override was introduced:

- Blue tiles are treated as high-cost nodes instead of forbidden nodes.
- Logic:
  - Avoid revisiting blue tiles if alternative paths exist.
  - Allow revisiting only when no other valid path is available.

### Result

- Maintains rule compliance and efficiency.
- Prevents deadlocks in constrained maze configurations.
- Improves robustness of exploration.

## 2. Botched Turn Recovery

During testing, inconsistent turning behavior was observed:

- The robot occasionally stops at incorrect angles (e.g., ~45° instead of 90°).
- Likely causes:
  - Motor power fluctuations
  - Surface inconsistencies
  - IMU drift

### Implementation

A new state was introduced in the robot state machine:

- BOTCHED_TURN

### Detection

The system detects a failed turn when:

- The robot's heading is not close to a cardinal direction after a turn.
- Uses headingToCardinal() to evaluate deviation.

### Correction Strategy

When triggered:

1. Determine the nearest cardinal direction.
2. Rotate to correct orientation.
3. Resume normal execution (EXECUTE_MOVE state).

### Design Considerations

- Does not reset navigation state (position, direction, map remain consistent).
- Ensures continuity in BFS and exploration logic.

### Result

- Eliminates accumulated orientation errors.
- Improves reliability of long navigation sequences.
- Reduces cascading navigation failures.

## 3. Navigation Logic Completion

The navigation system was refined to ensure full autonomy and stability:

### Key Improvements

- Fixed logical inconsistencies in movement decision flow.
- Ensured correct priority ordering:
  - Unvisited + open tiles
  - Visited but valid tiles
  - Backtracking (BFS)

### Integration with Tile States

- Tile attributes now include:
  - Walls
  - Visited state
  - Special tiles (black, blue, etc.)

### Behavior Enhancements

- Avoids black tiles (treated as obstacles per rules).
- Handles blue tiles with conditional revisiting logic.
- Maintains consistent map updates for BFS.

### Result

- Stable exploration without loops or stalls.
- Better handling of edge cases (dead ends, constrained paths).
- Fully functional autonomous navigation aligned with competition requirements.

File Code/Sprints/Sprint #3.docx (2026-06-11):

Sprint #3:

Goals:

1. Our number one priority for this sprint is to get the second robot to function, being better than the previous robot in terms of reliability.
2. Explore the option of PCB design
3. Possibly explore the option of using Claude code to improve the code that has been described, as in theory it should never work, but it does somehow.

What We Did

Robot 2 Progress: The main priority this sprint was getting the second robot functional and more reliable than the first. We made significant progress, the robot is mostly built, and the only remaining task is wiring and small reliability issues like the MUX breaking. We identified and resolved a short circuit in the Arduino that was being caused by the stepper motor, which was a reliability issue we needed to address before fully completing the wiring for this robot. For the final wiring setup, we're currently deciding between two options. The first option is to redesign the chassis so the protoboard and Arduino can be mounted as a stack. This would be the cleaner long-term solution, since the current vertical mount messes up the pin layout on the Arduino, making the bottom Dupont connectors difficult to seat properly and prone to falling out. The second option, if we don't have time for a chassis redesign, is to hot glue all the pins on the Arduino as an extra layer of protection to make sure nothing comes loose on competition day. We'll decide based on how much time we have left before the competition.

PCB Design We looked into the possibility of designing a custom PCB to replace the protoboard setup. We reached out to some G12 Computer Engineering students for help, and Leo Li offered to assist with the design work. However, after discussing it as a team, both Arthur and I agreed that with the competition approaching, our focus needs to stay on getting the current robot working reliably. Taking on a PCB design at this stage would be too much of a risk. The plan is to revisit this for next year's robot, where we can take the time to do it properly from the start. Depending on the time we have and if we are accepted, we might revisit this option

Code Improvements: The existing code we had wasn’t fully perfect and had small issues. Rather than trying to patch it further, we used Claude Code to do a full overhaul of the repository. This resulted in over 140 edits and changes across the codebase, cleaning up the logic and making it much more readable. We'll continue testing the updated code to see its reliability before fully committing to it for competition. If it works, this would be a significant improvement for reliability going forward.


Documentation: We continue to finalize and are preparing to submit our documentation to the international committee via GitHub.

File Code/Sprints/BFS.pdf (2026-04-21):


## Node Map created using https://csacademy.com/app/graph_editor/

# S-1 Sprint 1: Pathfinding Algorithm

# Goal:

The goal is to create a 2d path-finding code on a simulated test map that will allow us to return from any point in the maze to a checkpoint or the beginning.

# Research:

The most common pathfinding algorithms are DFS, BFS, and A*.

# DFS

## https://www.geeksforgeeks.org/dsa/depth-first-search-or-dfs-for-a-graph/

In DFS (or Depth First Search) for a graph, the algorithm traverses through all possible paths of through adjacent node before travelling to the next adjacent node. DFS will always use the first found path and contains a visited[] array to avoid revisiting nodes.

## Example:

In this example, we start from node 0 and the goal is to reach node 4.

## Data: [[0, 1], [0, 2], [1, 2], [2, 3], [2, 4]]


For this example, we begin by traversing from node 0 to node 1, and from node 1 the only possible move is to node 2. At node 2, there are two adjacent nodes: 3 and 4. We move to node 3, which has no unvisited neighbors, so we backtrack to node 2. Finally, we proceed to node 4, which is our goal, at which point the traversal ends.

From this example, we can see that although DFS finds a valid path between two nodes, it does not necessarily find the most optimal one. Instead, it returns the first valid path it encounters. This does not achieve the goal we have set but is the easiest to implement.

# BFS

## https://www.geeksforgeeks.org/dsa/breadth-first-search-or-bfs-for-a-graph/

In BFS (Breadth First Search) for a graph, the algorithm traverses all nodes adjacent from the first node, then moves onto the next node. BFS traverses the whole graph, contains a visited[] array to avoid revisiting nodes, and contains a queue[] array to keep track of the order in which nodes should be processed.

## Example:

Using the same example from the DFS, our goal is to traverse from node 0 to node 4.


Starting at node 0, nodes 1 and 2 are added to the queue, and node 0 is marked as visited. Next, node 1 is has its adjacent nodes either already visited or already in the queue, so no new nodes are added, and node 1 is marked as visited. Then, node 2 is processed, and it adds nodes 3 and 4 to the queue because nodes 0 and 1 have already been visited. Node 3 is then processed but has no unvisited neighbors. Finally, node 4 is reached, which is the target node, so the traversal ends.

A*

A* (A-star) search finds the most optimal path by considering both the distance traveled and an to the goal. It uses the formula f(n) = g(n) + h(n), where g(n) is the cost from the start node and h(n) is the estimated cost to the goal. At each step, A* selects the node with the lowest total cost f(n), ensuring that it prioritizes shorter paths. It keeps track of visited nodes and uses a priority queue to decide which node to explore next.

# Our choice

Between the three algorithms, the choice came down to BFS and A. We chose BFS because it was sufficient for the RoboCup maze challenge, while A did not offer significant additional benefits beyond handling weighted costs for certain tiles (such as blue tiles, ramps, or obstacles).

# Ideation:

I used a deque as the queue, along with 2D vectors to track visited nodes and parent nodes for path reconstruction. The algorithm starts by adding the starting position to the queue and marking it as visited. While the queue is not empty, it removes the front node and checks if it is the goal. If not, it adds all valid neighboring nodes to the queue. For debugging, I print each visited node and every node added to the queue. After the search, I print the visited array, and after reconstructing the path, I print the final path coordinates.

# Prototype:

# Version 1

#include <iostream>

#include <vector>

#include <deque>

using namespace std;

vector<pair<int,int>> BFS(pair<int,int> currentpos, vector<vector<bool>> map){ //define queue, visited & path arrays
deque<pair<int,int>> queue = {};
size_t rows = map.size();
size_t columns = map[0].size();
vector<vector<bool>> visited(rows, vector<bool>(columns, false)); vector<pair<int,int>> path = {};
queue.push_back(currentpos);

//search
while(queue.size() > 0){ // While there is an element in queue.
//mark as visited, print for debugging. visited[queue[0].first][queue[0].second] = true;
cout << "visting: " << queue[0].first << "," << queue[0].second << endl;

for(int i = 0; i < 4; i++){ //for each direction
int nx = queue[0].first + dir[i][0];
int ny = queue[0].second + dir[i][1];
if(nx < map.size() && ny < map[0].size() && nx >= 0 && ny >= 0){ //check if in bounds
if(!visited[nx][ny] && !map[nx][ny]){ //check if the position is valid and not visited
//
queue.push_back(pair<int,int>(nx,ny));
cout << "queue added: " << nx << "," << ny << endl; }

This is the first version of the code. It uses a 2D boolean vector as the test map and does not include path reconstruction. The BFS implementation works correctly and visits all valid nodes.

# Version 2

}
}
queue.pop_front();
}
cout << "done search" << endl; //reconstruct (unfinished) return path;
}

int main()
{
//2d map array, false tiles are traversable. vector<vector<bool> map = { {false,false,false},
{false,true,false},
{false,false,true},
{true,false,false},
}
}

#include <iostream>

#include <vector>

#include <deque>

using namespace std;

const int MAP_SIZE = 20;

int dir[4][2] = { {1,0}, {-1,0}, {0,1}, {0,-1} };

deque<pair<int,int>> BFS(pair<int,int> currentpos, vector<vector<bool>> map, pair<int,int> endpos) {
//define queue, visited & path arrays
deque<pair<int,int>> queue;

size_t rows = map.size();
size_t columns = map[0].size();

vector<vector<bool>> visited(rows, vector<bool>(columns, false)); deque<pair<int,int>> path;
vector<vector<pair<int,int>>> prev(MAP_SIZE, vector<pair<int,int>>(MAP_SIZE));

queue.push_back(currentpos);

// search
while (queue.size() > 0) { // While there is an element in queue. //mark as visited, print for debugging.

visited[queue[0].first][queue[0].second] = true;

int x = queue[0].first;
int y = queue[0].second;

cout << "visiting: " << x << ", " << y << endl;

for (int i = 0; i < 4; i++) { //for each direction int nx = x + dir[i][0];
int ny = y + dir[i][1];

if (nx < map.size() && ny < map[0].size() && nx >= 0 && ny >= 0) { //check if in bounds
if (!visited[nx][ny] && map[nx][ny]) { //check if the position is valid and not visited
queue.push_back(pair<int,int>(nx, ny));
// cout << "queue added: " << nx << ", " << ny << endl;
prev[nx][ny] = pair<int,int>(x, y);
}
}
}
//remove element from queue queue.pop_front();
}

// reconstruct -> essentially, each element contains coordinates that lead to the next tile, allowing us to retrace our steps
path.push_front(endpos);
pair<int,int> curr = prev[endpos.first][endpos.second];

while (true) {
path.push_front(curr);
curr = prev[curr.first][curr.second];

if (path[0] == currentpos) {
break;
}
}

cout << endl << "done search" << endl << endl;

return path;
}

int main() {
//2d map array, false tiles are traversable. vector<vector<bool>> map = {
{false, false, false},
{false, true, false},
{false, false, true},
{true, false, false}
};

This version adds path reconstruction and returns the final path, and on the simple test map it consistently produces the fastest path. However, it does not implement the actual tilemap system defined by my teammates, so it is not fully integrated with the project’s map structure. It also has a performance issue because visited nodes are not marked correctly at the right time, as they should be marked as visited as soon as they are added to the queue rather than when they are processed, which leads to repeated node insertions and significantly slows down the algorithm.

# Final Design:

deque<pair<int,int>> path = BFS(pair<int,int>(0,0), map, pair<int,int>(3,2));

//print path for debugging.
cout << "Path: " << endl;
for (int i = 0; i < path.size(); i++) {
cout << path[i].first << ", " << path[i].second << endl; }
}

#include <iostream>

#include <vector>

#include <deque>

#include <utility>

using namespace std;

enum Direction {
NORTH = 0,
EAST = 1,
SOUTH = 2,
WEST = 3
};

enum TileTypes {
BLANK = 0,
BLUE = 1,
BLACK = 2
};

template <unsigned size>
class Bitset
{
private:
static constexpr unsigned W = 8; // bits per uint8_t static constexpr unsigned WORDS = (size + W - 1) / W;

unsigned char mem[WORDS]{}; // zero-initialized

public:
bool get(unsigned i) const
{

if (i >= size) return false; | // or throw/assert
const unsigned word = i / W;
const unsigned bit = i % W;
return (mem[word] >> bit) & 0x1u;
}

void set(unsigned i, bool b)
{
if (i >= size) return; | // or throw/assert
const unsigned word = i / W;
const unsigned bit = i % W;
const unsigned char mask = static_cast<unsigned char>(1u << bit);

if (b) mem[word] |= mask;
else mem[word] &= static_cast<unsigned char>(~mask);
}
};

struct Tile {
//bool discovered;
//bool fullyExplored;

private:
//first 4 bit is wall, last 4 bit is edge //set amount of bits
Bitset<16> bitset;
TileTypes tileType;
public:
//get and set functions
bool getWall(unsigned dir) {
return bitset.get(dir);
}
void setWall(unsigned dir, bool stat) { bitset.set(dir, stat);
}
//+4 is index to the target bit
bool getEdge(unsigned dir) {
return bitset.get(dir + 4);
}
void setEdge(unsigned dir, bool stat) { bitset.set(dir + 4, stat);
}
bool getDiscovered() {
return bitset.get(8);
}

void setDiscovered(bool stat) { bitset.set(8, stat);
}
bool getFully() {
return bitset.get(9);

}
void setFully(bool stat) { bitset.set(9, stat);
}
TileTypes getType() {
return tileType;
}
void setType(TileTypes type) { tileType = type;
}
bool getVictim() {
return bitset.get(10);
}
void setVictim(bool vic) { bitset.set(10, vic);
}

//bool wall[4];
//bool edge[4];

//bool tileType
//bool victim;

//Tile(); // constructor
};

int dir[4][2] = {
{0, 1},
{1, 0},
{0, -1},
{-1, 0}
};

const int MAP_SIZE = 20;
Tile mapGrid[MAP_SIZE][MAP_SIZE];

void initializeMap(){
for (int x = 0; x < MAP_SIZE; x++) { for (int y = 0; y < MAP_SIZE; y++) { mapGrid[x][y].setDiscovered(false); mapGrid[x][y].setFully(false);
for (int d = 0; d < 4; d++) {
| if (x % 3 == 0 && y % 3 == 0) {
| mapGrid[x][y].setWall(d, true); }
| mapGrid[x][y].setEdge(d, false);
}
mapGrid[x][y].setType(BLANK);
}
}
}

deque<pair<int,int>> BFS(pair<int,int> currentpos, Tile mapGrid[MAP_SIZE][MAP_SIZE], pair<int, int> endpos) {
//define queue, visited & path arrays
deque<pair<int, int>> queue = {};
size_t rows = MAP_SIZE;
size_t columns = MAP_SIZE;
vector<vector<bool>> visited(rows, vector<bool>(columns, false)); deque<pair<int, int>> path = {};
vector<vector<pair<int, int>>> prev(MAP_SIZE, vector<pair<int,int>>(MAP_SIZE)); queue.push_back(currentpos);

//search
while (queue.size() > 0) { // While there is an element in queue. //mark as visited, print for debugging.
int x = queue[0].first; int y = queue[0].second;
//cout << "visting: " << x << "," << y << endl;

for (int i = 0; i < 4; i++) { //for each direction
int nx = x + dir[i][0];
int ny = y + dir[i][1];
if (nx < rows && ny < columns && nx >= 0 && ny >= 0) { //check if in bounds
if (!visited[nx][ny] && !mapGrid[nx][ny].getWall(i)) { //IMPORTANT: ADD MORE CONDITIONALS HERE
queue.push_back(pair<int, int>(nx, ny));
visited[nx][ny] = true;
//cout << "queue added: " << nx << "," << ny << endl;
prev[nx][ny] = pair<int, int>(x, y);
//cout << "at: " << nx << "," << ny << " added: " << x << "," << y << endl;
}
}
}
//remove element from queue queue.pop_front();
}
for (int i = 0; i < visited.size(); i++) {
for (int j = 0; j < visited[0].size(); j++) { cout << visited[i][j] << " ";
}
cout << endl;
}
// reconstruct -> essentially, each element contains coordinates that lead to the next tile, allowing us to retrace our steps
path.push_front(endpos);
pair<int, int> curr = prev[endpos.first][endpos.second];
while (true) {
//cout << curr.first << "," << curr.second << endl; path.push_front(curr);
curr = prev[curr.first][curr.second];
if (path[0] == currentpos) {
break;
}

The pathfinding system was built using a BFS (breadth-first search) approach on a 20×20 tilemap created with a Tile object array created by teammates. A direction array was defined to handle movement in the four cardinal directions during the search. The BFS function takes the current position, target position, and tilemap as inputs and returns a deque of integer pair positions representing the final path. Inside the function, a queue is used to manage exploration order, along with a 2D boolean visited array to track explored tiles and prevent revisiting, and a 2D vector called prev to store each node’s parent for later path reconstruction. The algorithm begins by pushing the starting position into the queue, then repeatedly processes the front of the queue by checking its four neighboring tiles using the direction array. If a neighbor is within bounds, not visited, and not blocked by a wall, it is marked as visited, added to the queue, and its previous node is recorded in prev. This continues until the search completes, after which the path is reconstructed by tracing backwards from the target using the prev array, building a deque from end to start that represents the final shortest path.

}
//cout << endl << "done search" << endl << endl; return path;
}

int main()
{
/*vector<vector<bool>> map = { {false, false, false},
{ false, true, false },
{ false, false ,true },
{ true, false ,false }
};*/

initializeMap();

deque<pair<int, int>> path = BFS(pair<int, int>(0, 0), mapGrid, pair<int,int>(4,4));

//print path for debugging.
cout << "path: " << endl;
for (int i = 0; i < path.size(); i++) {
cout << path[i].first << "," << path[i].second << endl; }
}


The code successfully performs pathfinding on a 20×20 test grid with no restrictions, and it completes the search quickly and correctly. In the map output, the tiles marked with 1 represent all the nodes that were visited during the search process, while the second output shows the final travelled path leading to the target position at (4,4). Overall, this indicates that the algorithm is working as intended.

It also continues to work correctly when walled nodes are added to the test map, which shows that the pathfinding logic is handling obstacles properly and the algorithm successfully avoids the blocked areas while still finding a valid route to reach the target.

# Conclusion

In conclusion, the system works correctly and reliably produces valid paths using BFS, even when obstacles are introduced into the tilemap. It successfully explores the grid, tracks visited nodes, and reconstructs the shortest path using the prev array without issues. To improve this in the future, the algorithm could be upgraded to A* pathfinding, which would make the search faster and more efficient as well as the implementation of weighted costs, such as higher movement penalties for blue tiles or elevation changes.

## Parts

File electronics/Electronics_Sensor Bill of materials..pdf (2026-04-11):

Carobot V3 | Motor Shield | Issues: Is connected to I2C( Need to jump cables) Has an allcall address of 0x70, which conflicts with the multiplexer. | Documentation https://learn.carobot.ca/guide/motor-shield-v3 (https://learn.carobot.ca/guide/motor-shield-v3)

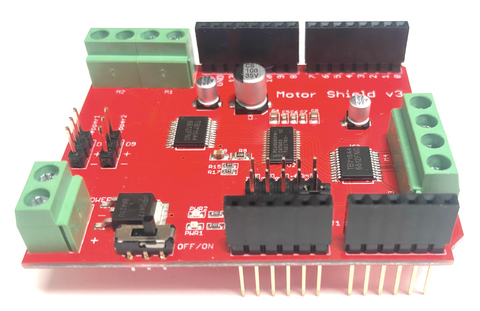
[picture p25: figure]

TCA9548A qwiic mux | I2C multiplexer | Address conflicts with Carobot. Pins get easily deformed | https://cdn.sparkfun.com/assets/f/0/4/b/3/tc a9548a.pdf (https://cdn.sparkfun.com/assets/f/0/4/b/3/tca9548a.pdf)

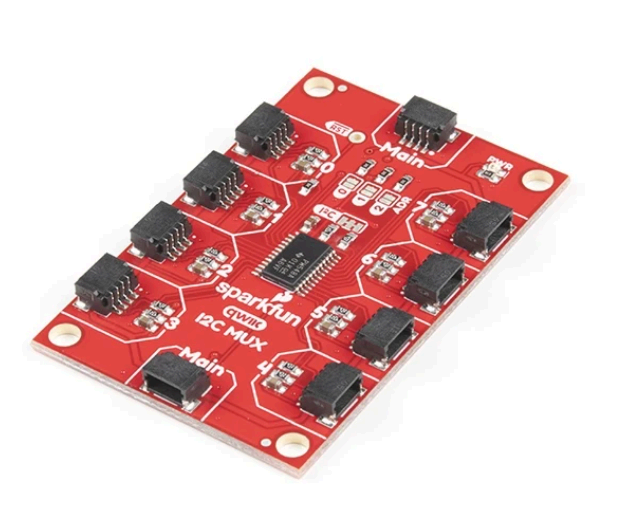
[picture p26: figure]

BNO055 absolute orientation sensor | IMU | The sensor has no reset: the heading is always global. The sensor has a 360 degree wraparound, which is sensitive to fluctuations. | https://cdn-shop.adafruit.com/datasheets/BST_BNO055_DS000_12.pdf (https://cdn-shop.adafruit.com/datasheets/BST_BNO055_DS000_12.pdf) code:https://adafruit.github.io/Adafruit_BNO055/html/class_adafruit___b_n_o055.html (https://adafruit.github.io/Adafruit_BNO055/html/class_adafruit___b_n_o055.html)

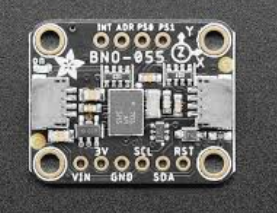
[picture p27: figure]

VL53L0X TOF sensor | TOF Lidar | The sensors I2C address is 0x29, which conflicts with TCS34725. Can’t handle below 30mm of range | https://learn.adafruit.com/adafruit-vl53l0x-m icro-lidar-distance-se nsor-breakout/overvie w (https://learn.adafruit.com/adafruit-vl53l0x-micro-lidar-distance-sensor-breakout/overview)

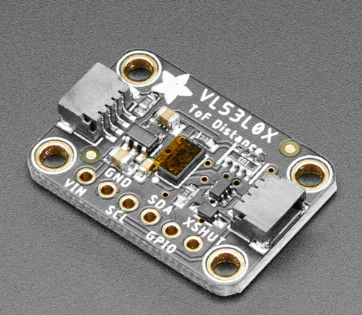
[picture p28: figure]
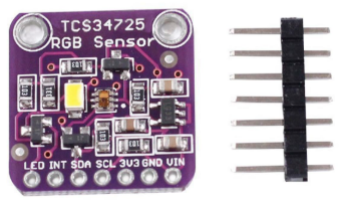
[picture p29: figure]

TCS34725 | Color sensor | Its unchangeable address conflicts with Vl53l0X. Measurement takes 50ms | https://adafruit.github.io/Adafruit_TCS34725/html/class_adafruit___t_c_s34725.html

195:1 Metal Gearmotor
20Dx44L mm 12V CB with
Extended Motor Shaft
| Motor | Extended shaft for encoder | https://www.pololu.com/product/3493
| Stepper motor | The motor itself is 5V, so you need a 5v buck. | https://lastminuteengineers.com/28byj48-st epper-motor-arduino-tutorial/

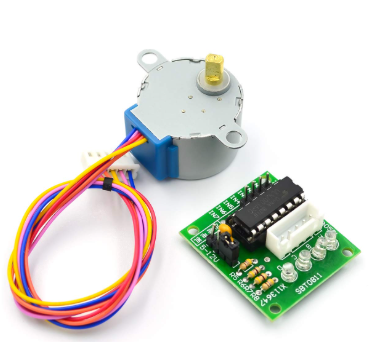
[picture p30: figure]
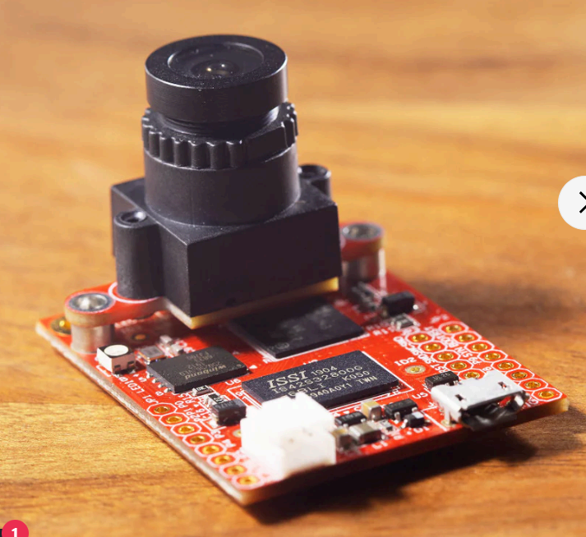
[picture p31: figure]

OpenMV H7 plus. | Camera | Memory can leak from power brownouts without and SD card. | https://docs.openmv.io/library/omv.image.h tml

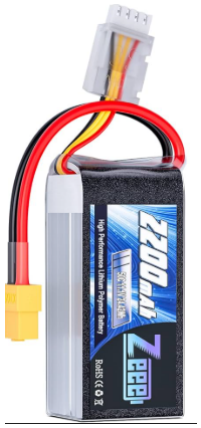
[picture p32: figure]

Lipo battery | ALWAYS unplug the robot before charging.

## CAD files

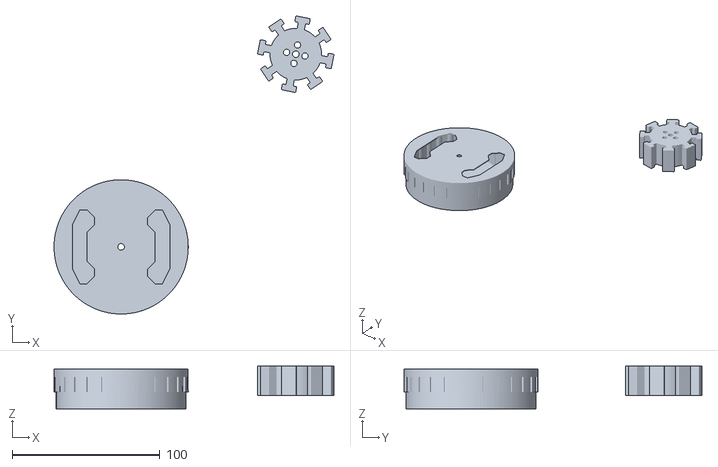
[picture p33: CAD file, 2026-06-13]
Fusion 360 designs/Silicone Wheel Casting Box V3.stl
189.8 x 202.0 x 29.0

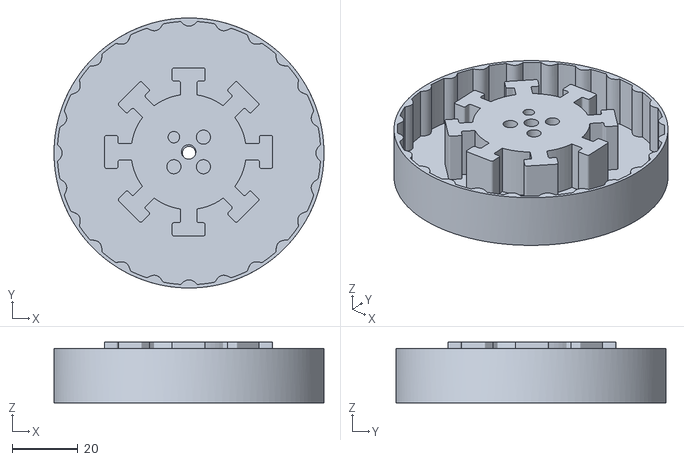
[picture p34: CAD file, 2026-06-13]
Fusion 360 designs/Silicone Wheel Casting Box Variation 4.stl
82.0 x 82.0 x 18.5

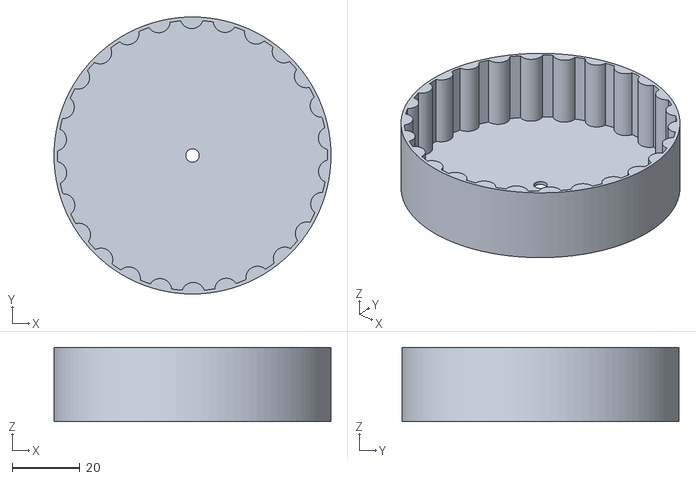
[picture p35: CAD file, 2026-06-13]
Fusion 360 designs/Breakable Silicone Casting box.stl
82.0 x 82.0 x 22.0

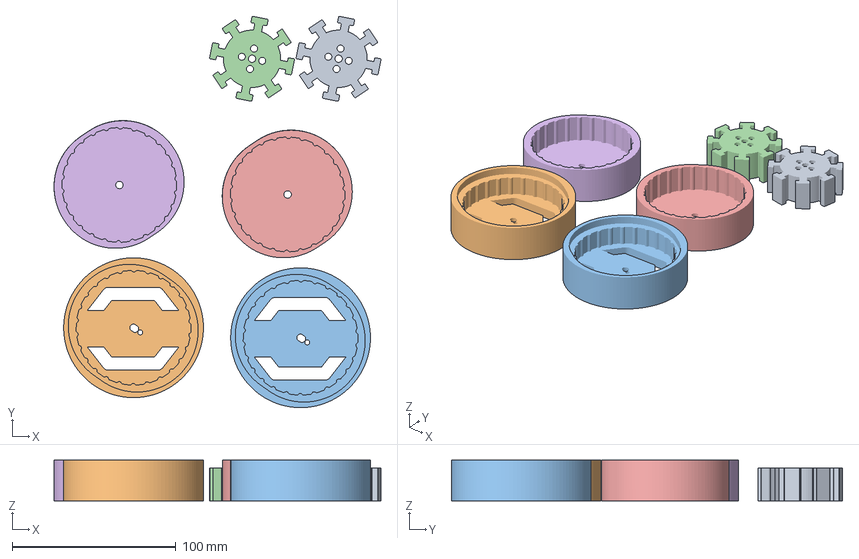
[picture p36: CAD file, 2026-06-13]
Fusion 360 designs/Reusable Casting Box V2.3mf
199.5 x 238.7 x 25.0 mm
Casting box wheel.stl_1 x 2
Casting box wheel.stl_2 x 2
Casting box wheel.stl x 2

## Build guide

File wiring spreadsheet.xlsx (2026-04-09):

RST | AREF
3V3 | GND |  | 5V | 5v
5V | 13 |  | 22 | 23 | Motors
GND | 12 |  | 24 | 25 | M1
GND | 11 |  | 26 | 27 | M2
Vin | 10 |  | 28 | 29 | M3
 | 9 |  | 30 | 31 | M4
A0 | 8 |  | 32 | 33
A1 | 7 |  | 34 | 35 | Cameras:
A2 | 6 |  | 36 | 37 | Left camera
A3 | 5 | encoder pin B | 38 | 39 | Right camera.
A4 | 4 | encoder pin B | 40 | 41
A5 | 3 | encoder pin A | 42 | 43
A6 | 2 | encoder pin A | 44 | 45 | I2C:
A7 | 1 |  | 46 | 47 | SDA
A8 | 0 |  | 48 | 49 | SCL
A9 |  |  | 50 | 51
A10 | TX3 | P0 | 52 | 53
A11 | RX3 | P1 | GND | GND
A12 | TX2 | P0
A13 | RX2 | P1
A14 | TX1
 | RX1
 | SDA 20 | SDA
 | SCL 21 | SCL

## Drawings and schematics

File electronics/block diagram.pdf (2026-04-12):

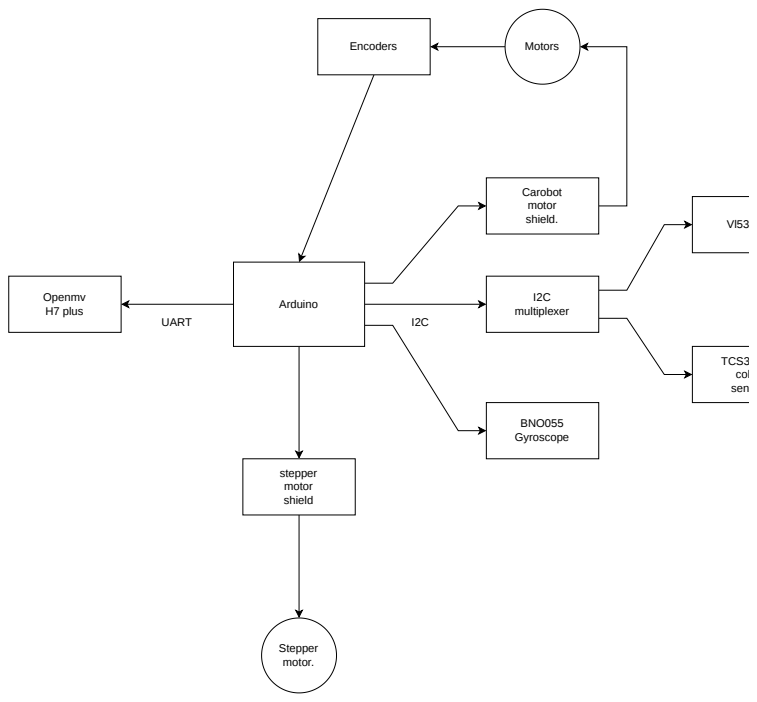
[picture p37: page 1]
Arduino; multiplexer; BNO055 Gyroscope; TCS3 col sen; Carobot motor shield.; Motors; stepper motor shield; Openmv H7 plus; Stepper motor.; Encoders; UART

3L0X

34725
olor
nsor

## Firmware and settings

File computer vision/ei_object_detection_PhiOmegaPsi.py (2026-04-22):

# Edge Impulse - OpenMV FOMO Object Detection Example
#
# This work is licensed under the MIT license.
# Copyright (c) 2013-2024 OpenMV LLC. All rights reserved.
# https://github.com/openmv/openmv/blob/master/LICENSE

import sensor, image, time, ml, math, uos, gc
import pyb
from pyb import UART
sensor.reset()                         # Reset and initialize the sensor.
sensor.set_pixformat(sensor.RGB565)    # Set pixel format to RGB565 (or GRAYSCALE)
sensor.set_framesize(sensor.QVGA)      # Set frame size to QVGA (320x240)
sensor.set_windowing((240, 240))       # Set 240x240 window.
sensor.skip_frames(time=2000)          # Let the camera adjust.
sensor.set_vflip(True) # the camera's upside down on the robot.
sensor.set_hmirror(True)
net = None
labels = None
min_confidence = 0.9
# initialize uart
uart = UART(1, 115200, timeout_char=100)\
# initialize GPIO
p = pyb.Pin("P3", pyb.Pin.OUT_PP)
# reduce exposure time for less blur
#sensor.set_auto_exposure(False, exposure_us=20000)  # ~8 ms
#thresholds
black_threshold = (0, 20, -128, 127, -128, 127)
red_threshold = (0, 100, 39, 127, -128, 127)
yellow_threshold = (0, 100, -60, 70, 0, 128)
green_threshold = (0, 100, -128, -3, -49, 45)
blue_threshold = (0, 100, -128, 127, -128, -23)
def in_threshold(L,A,B,c):
    if(c[0]<L<c[1] and c[2]<A<c[3] and c[4]<B<c[5]):
        return True
    else:
        return False
try:
    # load the model, alloc the model file on the heap if we have at least 64K free after loading
    net = ml.Model("trained.tflite", load_to_fb=uos.stat('trained.tflite')[6] > (gc.mem_free() - (64*1024)))
except Exception as e:
    raise Exception('Failed to load "trained.tflite", did you copy the .tflite and labels.txt file onto the mass-storage device? (' + str(e) + ')')

try:
    labels = [line.rstrip('\n') for line in open("labels.txt")]
except Exception as e:
    raise Exception('Failed to load "labels.txt", did you copy the .tflite and labels.txt file onto the mass-storage device? (' + str(e) + ')')

colors = [ # Add more colors if you are detecting more than 7 types of classes at once.
    (255,   0,   0),
    (  0, 255,   0),
    (255, 255,   0),
    (  0,   0, 255),
    (255,   0, 255),
    (  0, 255, 255),
    (255, 255, 255),
]

threshold_list = [(math.ceil(min_confidence * 255), 255)]

def fomo_post_process(model, inputs, outputs):
    ob, oh, ow, oc = model.output_shape[0]

    x_scale = inputs[0].roi[2] / ow
    y_scale = inputs[0].roi[3] / oh

    scale = min(x_scale, y_scale)

    x_offset = ((inputs[0].roi[2] - (ow * scale)) / 2) + inputs[0].roi[0]
    y_offset = ((inputs[0].roi[3] - (ow * scale)) / 2) + inputs[0].roi[1]

    l = [[] for i in range(oc)]

    for i in range(oc):
        img = image.Image(outputs[0][0, :, :, i] * 255)
        blobs = img.find_blobs(
            threshold_list, x_stride=1, y_stride=1, area_threshold=1, pixels_threshold=1
        )
        for b in blobs:
            rect = b.rect()
            x, y, w, h = rect
            score = (
                img.get_statistics(thresholds=threshold_list, roi=rect).l_mean() / 255.0
            )
            x = int((x * scale) + x_offset)
            y = int((y * scale) + y_offset)
            w = int(w * scale)
            h = int(h * scale)
            l[i].append((x, y, w, h, score))
    return l

clock = time.clock()
iterator = 0
while(True):

    clock.tick()
    iterator+=1
    img = sensor.snapshot().lens_corr(1.8)
    p.low()
    if iterator % 3==0:
        #continue
        img.to_grayscale()
        img.binary([(80,255)])

        blobs = img.find_blobs(
            [(0,20)],# must be a list of tuples
            pixel_threshold = 60,
            area_threshold=2500,
            merge=True
        )

        if blobs:
            uart.write("L")
        for b in blobs:
            width, height = b.w(), b.h()
            area = width*height
            filled_area = b.pixels()/area
            aspect = max(width,height)/min(width,height)

            if filled_area > 0.6 or filled_area<0.15:

                continue
            elif aspect > 1.6:

                continue
            elif area > 20000:
                continue
            else:
                img.draw_rectangle(b.rect(),0);

    else:
        circles = img.find_circles(threshold = 3500, r_min = 50) # find circles
        if circles:
            uart.write("c")
            time.sleep_ms(350)
        for circle in circles:
            img.draw_circle(circle.x(),circle.y(),circle.r()) # draw the circle for debugging

            sum = 0
            for i in range(1,6):
                colorarray = [0,0,0,0,0];

                for j in range(1,30):
                    x = circle.x()+math.floor(circle.r()*0.18*i*math.cos(math.radians(12*j)))
                    y = circle.y()-math.floor(circle.r()*0.18*i*math.sin(math.radians(12*j))) # increment across each ring.



                    r, g, b = img.get_pixel(x,y)


                    L,A,B = image.rgb_to_lab(r,g,b)

                    if r+g+b<100 and in_threshold(L,A,B,black_threshold):

                        colorarray[0] += 1

                    elif r>b and g > b and abs(g-r)<50 and in_threshold(L,A,B,yellow_threshold):
                        colorarray[1]+=1
                    elif r>g and r>b and in_threshold(L,A,B,red_threshold):
                        colorarray[2]+=1
                    elif g>r and g>b and in_threshold(L,A,B,green_threshold):
                        colorarray[3]+=1
                    elif b>g and b>r and in_threshold(L,A,B,blue_threshold):
                        colorarray[4]+=1
                color = colorarray.index(max(colorarray)) # voting
                if color == 0:
                    print("black")
                    sum += -2
                elif color == 1:
                    print("yellow")
                    sum += 0
                elif color == 2:
                    print("red")
                    sum+=-1
                elif color == 3:
                    print("green")
                    sum += 1;
                else:
                    print("blue")
                    sum += 2
                img.draw_circle(circle.x(),circle.y(),math.floor(circle.r()*0.18*i))
        print(sum)
        if sum == 2:
            uart.write("H") # harmed victim
            p.high()
        elif sum == 1:
            uart.write("S") #stable victim
            p.high()
        elif sum == 0:
            uart.write("U") # unharmed victim.
            p.high()
        print("_____________")
    for i, detection_list in enumerate(net.predict([img], callback=fomo_post_process)):
        if i == 0: continue  # background class
        if len(detection_list) == 0: continue  # no detections for this class?
        if iterator%3==0:
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

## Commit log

2026-04-09 Create wiring spreadsheet.xlsx
    [wiring spreadsheet.xlsx]
2026-04-09 Revise Sprint1.md for clarity and image updates
    Updated images and improved layout for clarity and organization. Enhanced descriptions of chassis and suspension design changes.
2026-04-12 Add files via upload
    A diagram of the sensor architecture of our hybrid control system, which involves both a high-level( pathfinding, mapping) system and a low-level( black tile detection, PID) one.
2026-06-12 Enhance README with sensor details and images
    Added images and refined sensor descriptions in the README.
2026-06-13 Add files via upload
    Variations of the silicone wheel casting boxes between Theseus versions 1 and 2
    [Breakable Silicone Casting box.stl, Reusable Casting Box V2.3mf, Silicone Wheel Casting Box V3.stl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]
